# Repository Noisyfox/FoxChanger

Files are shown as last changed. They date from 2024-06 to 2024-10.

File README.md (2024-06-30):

# FoxChanger
[中文版点我](./README.chs.md)

Voron 2.4/Trident tool changer mod inspired by Prusa XL toolchanger.

No customized/homemade metal parts required, 100% off-the-shelf parts without any post-processing/modification, except for 3d-printed parts of course.

[Demo video](https://www.bilibili.com/video/BV1c142117zm)

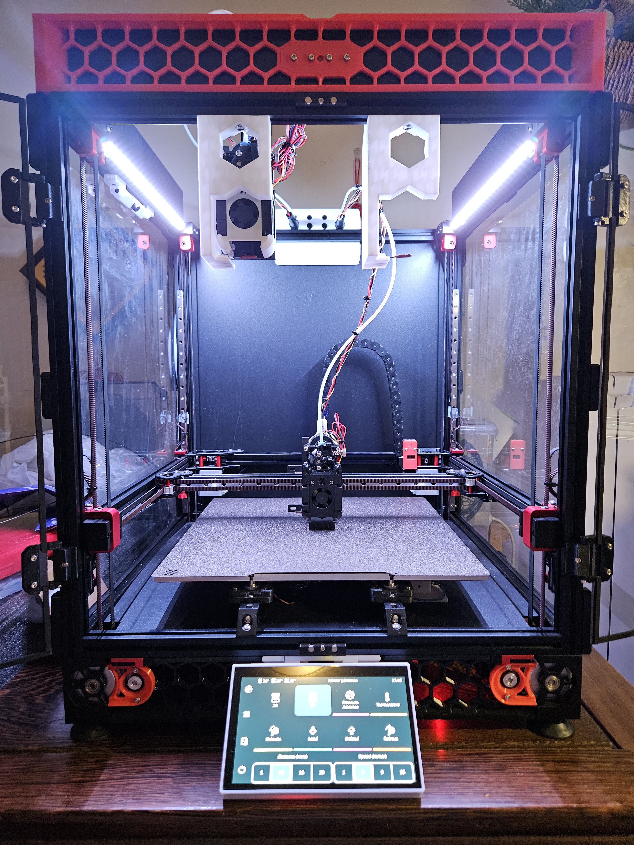
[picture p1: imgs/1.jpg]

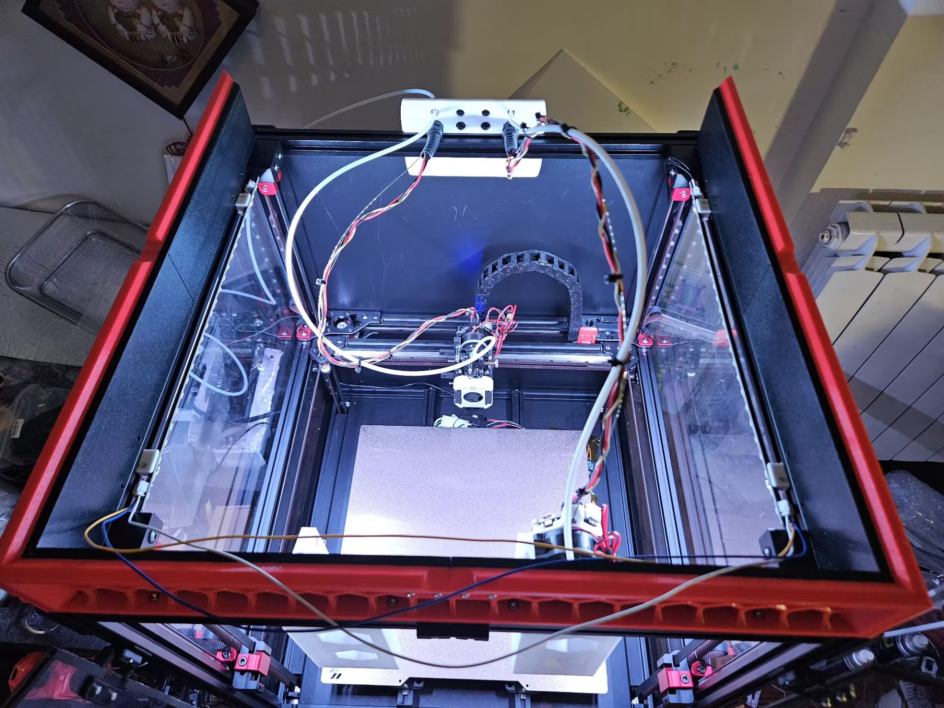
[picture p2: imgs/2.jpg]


# Credit
This project is based on the following excellent works:
- [VORON Design](https://vorondesign.com/)
- [Klipper](https://www.klipper3d.org/)
- [Prusa Research](https://www.prusa3d.com/) for their Prusa XL, that created this toolhead locking mechanism
- [Viesturs Zariņš](https://github.com/viesturz) for tapchanger, klipper-toolchanger and nozzle align
- [3DUnplugged](https://www.youtube.com/channel/UCr8K1tva2CaEhyqNyaEjq_w) for his excellent analysis on Prusa XL's toolchanger, and his DAKSH tool changer V2 design
- [diedirk](https://www.printables.com/@diedirk_282928) for Sherpa Zero ECAS extruder
- [KayosMaker](https://github.com/KayosMake) for canboard mount
- [chirpy2605](https://github.com/chirpy2605) for the DragonBurner toolhead

# Hardware Overview
This mod contains the following 3 parts:
- Toolchanger: toolhead mount and dock
- Piezo bed sensor: piezo based z homing sensor under heatbed
- Nozzle align probe: micro-switch based multi-toolhead alignment tool

## Toolchanger
Currently this mod is designed around the Dragon Burner. Other toolheads might be used with different mount, however the size constraint needs to be considered. Also there will be no space to install the z proble inside the toolhead, or use Voron Tap for z homing, so a BambuLab P1/X1-like heatbed piezo sensor is used instead.

__Note: All shop links are not affiliate links! Just for examples!__

- Unmodified [Dragon Burner](https://github.com/chirpy2605/voron/tree/main/V0/Dragon_Burner), except the mount
- A slightly modified version of [Sherpa Zero ECAS extruder](https://www.printables.com/model/495935-sherpa-zero-ecas), thicker to support cloned BMG gears without grinding the gear shaft
- [Fly SHT-36 V2 CAN board](https://mellow-3d.github.io/fly-sht36_v2_general.html)
- A slightly modified version of [KayosMaker's CANboard_Mounts](https://github.com/KayosMaker/CANboard_Mounts), with a grove to attach the umbilical steel wire
- X carriage
  - 6\*8\*3(inner\*outer\*height) sintered porous bronze bearing (x3)
  - 2\*25(PHi\*length) stainless steel round head cylindrical positioning pin (x4)
  - 1\*8(PHi\*length) stainless steel round head cylindrical positioning pin (x4)
  - 0.3\*3\*5(PHi\*outer\*length) 304 stainless steel spring (x4)
  - M3\*8 SHCS (x4)
  - M3\*12 SHCS (x2)
  - M3 heat set insert (x2)
- Toolhead mount
  - 1\*2\*8\*1(short\*long\*width\*thickness) steel angle with 3mm holes (x2)
  - 6\*4\*8\*M3 cone head positioning pin (x3)
  - M3\*2\*5(thread\*length\*outer diameter) brass round column with threaded throughhole (x4)
  - M3\*5 set screw DIN (x2)
  - 3\*30(PHi\*length) stainless steel round head cylindrical positioning pin (x2)
  - 6\*3(PHi\*thickness) round magnet (x2)
  - M3\*6 FSHC (x5)
  - M3 heat set insert (x4)
- Dock
  - 3\*50(PHi\*length) stainless steel round head cylindrical positioning pin (x2)
  - 6\*3(PHi\*height) round magnet (x2)
  - 0.4\*5\*15(thickness\*width\*length) 301 stainless steel strip
  - [nozzle pad mold from TapChanger](https://github.com/viesturz/tapchanger/tree/f6a354f5bf93b9d8721f022794a41ad3e51c5828/Dock/Jigs)
  - [High temperature silicone adhesive](https://www.aliexpress.com/item/1005002418580570.html)
  - M3\*6 FSHC (x2)
  - M3\*12 SHCS (x1)
  - M5\*10 BHCS (x1)
  - M3 heat set insert (x2)
  - M3 T-nut (x1)
  - M5 T-nut (x1)

Note: Due to the extended latch, the gantry left XY joint needs to be modified, or use the CNC version like I did.

## Piezo bed sensor
Heatbed z probe sensor made with 4 20mm piezo disks and an off-the-shelf analog vibration sensor board.

- Piezoelectric Shock Tap Sensor, Vibration Switch Module like [this one](https://www.amazon.com/Rakstore-Piezoelectric-Vibration-piezoelectric-Percussion/dp/B09GX97X6B)
- 20mm piezo disk (x4)
- 6\*8\*3(inner\*outer\*height) sintered porous bronze bearing (x8)
- 6\*15(PHi\*length) linear guide rail (x8)
- M3\*8 SHCS (x4)
- M3\*10 SHCS (x8)
- M3 heat set insert (x8)
- M3 T-nut (x4)

## Nozzle align probe

- 6mm stainless steel ball (or Si3N4 ball like I'm using) (x1)
- Omron D2FC-f-7N micro-switch, or any other compatiable ones (x1)
- 6\*8\*3(inner\*outer\*height) sintered porous bronze bearing (x1)

# Print
Print most of the parts with the same settings as what Voron recommended.

I print most parts in PETG, except the latch, x carriage frame, dragon burner back plate and piezo probes which are printed in PETG-CF.

Print the latches in 100% infill and Arachne wall generator.

Most of the parts are designed to be printed without support, and some of them have built-in support.

I'll provide recommended print orientation inside each part's readme.

# Support this project
If you like my work, feel free to by me a coffe:



[afdian](https://afdian.net/a/noisyfox)

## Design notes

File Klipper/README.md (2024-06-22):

[中文版点我](./README.chs.md)

# Klipper setup

The config here is just the setup I'm using.

## Installing

- Install [toolchanger extension](https://github.com/viesturz/klipper-toolchanger/)
- Use the config as a guide for your own config

## Orca Slicer config

### Printer settings
- Cooling tube length: 15
- Cooling tube position: 35
- Filament parking position: 35
- Enable filament ramming: false
- Change filament G-code:
```
M104 T[current_extruder] S[old_filament_temp] ; fix issue that current temp is set to next filament during unload
M104 T[next_extruder] S[new_filament_temp] ; preheating the next toolhead

M204 S9000
{if toolchange_count > 1 && (z_hop_types[current_extruder] == 0 || z_hop_types[current_extruder] == 3)}
G17
G2 Z{z_after_toolchange + 0.4} I0.86 J0.86 P1 F10000 ; spiral lift a little from second lift
{endif}

{if toolchange_count > 1}
T[next_extruder] X=[x_after_toolchange] Y=[y_after_toolchange] Z=[z_after_toolchange]
G1 X[x_after_toolchange] Y[y_after_toolchange] Z[z_after_toolchange] F12000 ; make gcode preview happy
{else}
T[next_extruder]
{endif}
```
- Start Gcode:
```
M104 S0
M140 S0
PRINT_START EXTRUDER=[nozzle_temperature_initial_layer] BED=[bed_temperature_initial_layer_single] CHAMBER=[chamber_temperature] MESH_MIN={adaptive_bed_mesh_min[0]},{adaptive_bed_mesh_min[1]} MESH_MAX={adaptive_bed_mesh_max[0]},{adaptive_bed_mesh_max[1]} MESH_ALGO=[bed_mesh_algo] MESH_PROB_COUNT={bed_mesh_probe_count[0]},{bed_mesh_probe_count[1]} TOOL=[initial_extruder]
```

### Filament settings
- Delay after unloading: 2

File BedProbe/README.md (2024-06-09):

[中文版点我](./README.chs.md)

## Install
1. Install the linear guide rail on the bottom part. Use fitting.STEP to help pushing the rails in.
2. Install the heat set and bronze bearing. Use ring_pusher.STEP from toolchanger to help pushing the bearing in. Avoid using any metal tools to push the bearing in, otherwise you might damage it and increasing the friction!
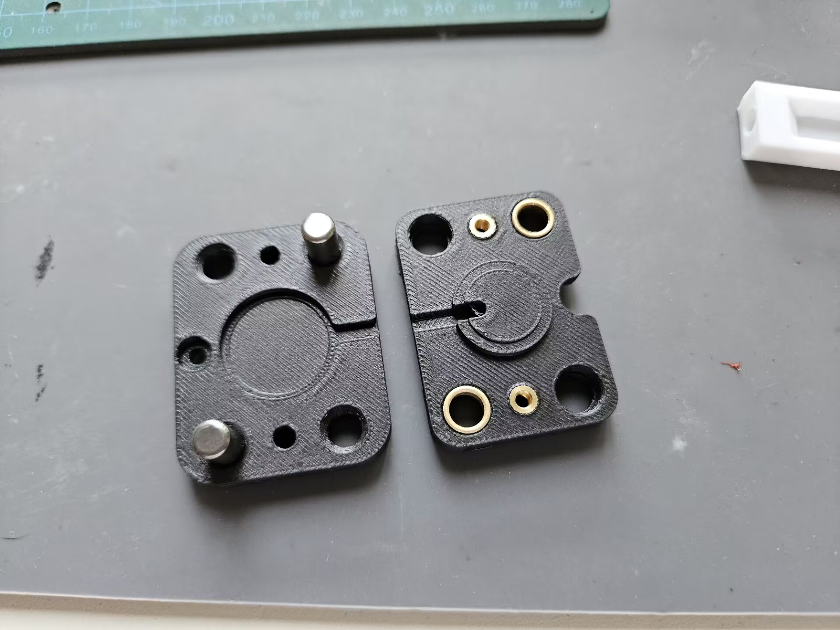
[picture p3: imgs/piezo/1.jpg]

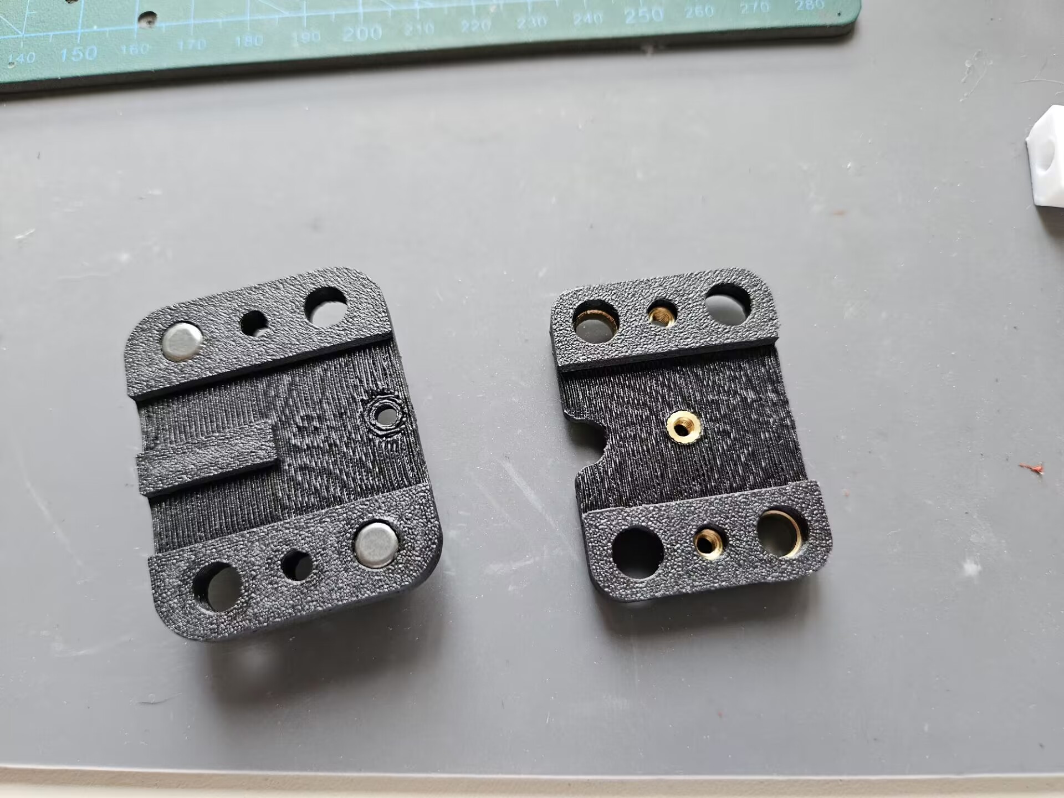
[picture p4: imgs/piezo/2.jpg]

3. Put the piezo disk in, make sure the ceramic side faces upwards
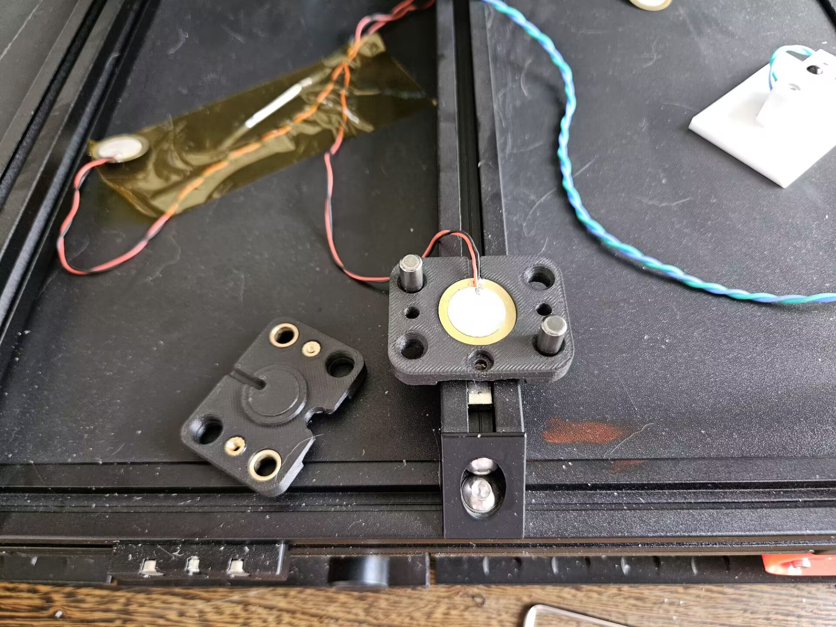
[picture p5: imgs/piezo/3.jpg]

4. Put on M3x10 screws. Do not tighten! The screws are here to avoid heatbed falling down when you flip the printer over, do not apply any extra pressure to the sensor.
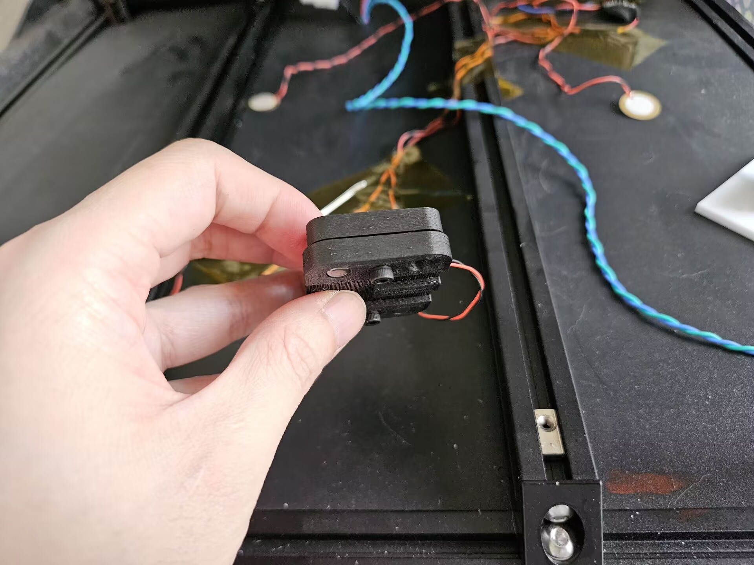
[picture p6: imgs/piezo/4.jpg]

5. Mount the sensors on the extrusions and connect the wires
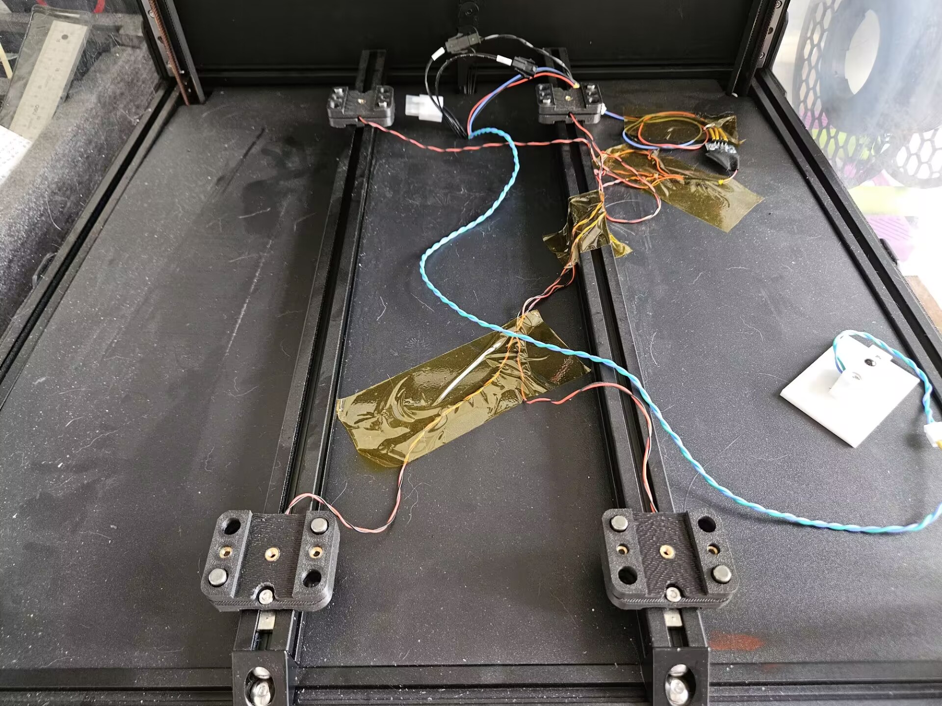
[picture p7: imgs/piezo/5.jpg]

6. Put the heatbed on
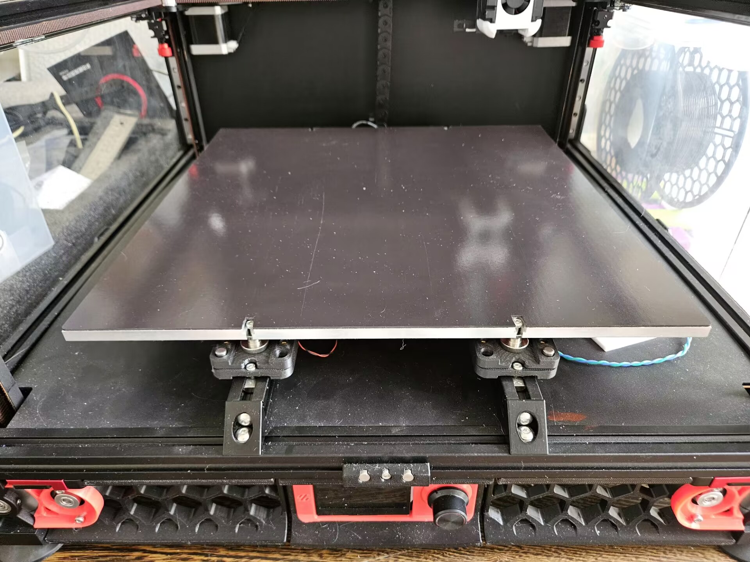
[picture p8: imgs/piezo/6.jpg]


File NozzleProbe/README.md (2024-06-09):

[中文版点我](./README.chs.md)

[Demo video](https://www.bilibili.com/video/BV1hH4y1u7oX/)

This is a simple but accurate nozzle alignment probe that works with [viesturz's NozzleAlign](https://github.com/viesturz/NozzleAlign).

Just clamp it to your heatbed and follows the instructions [here](https://github.com/viesturz/NozzleAlign/blob/main/README.md#klipper-integration).

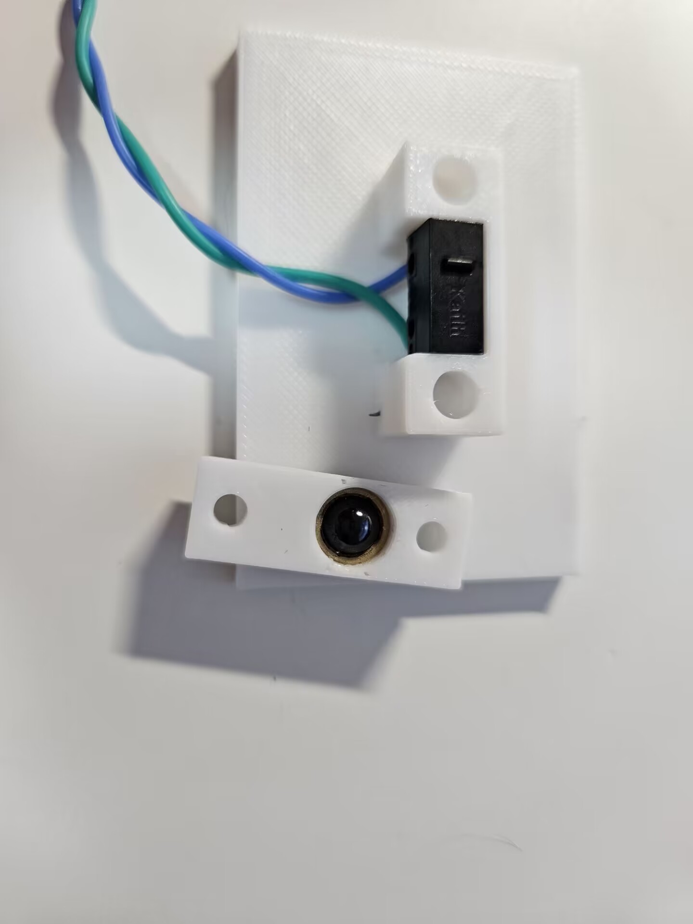
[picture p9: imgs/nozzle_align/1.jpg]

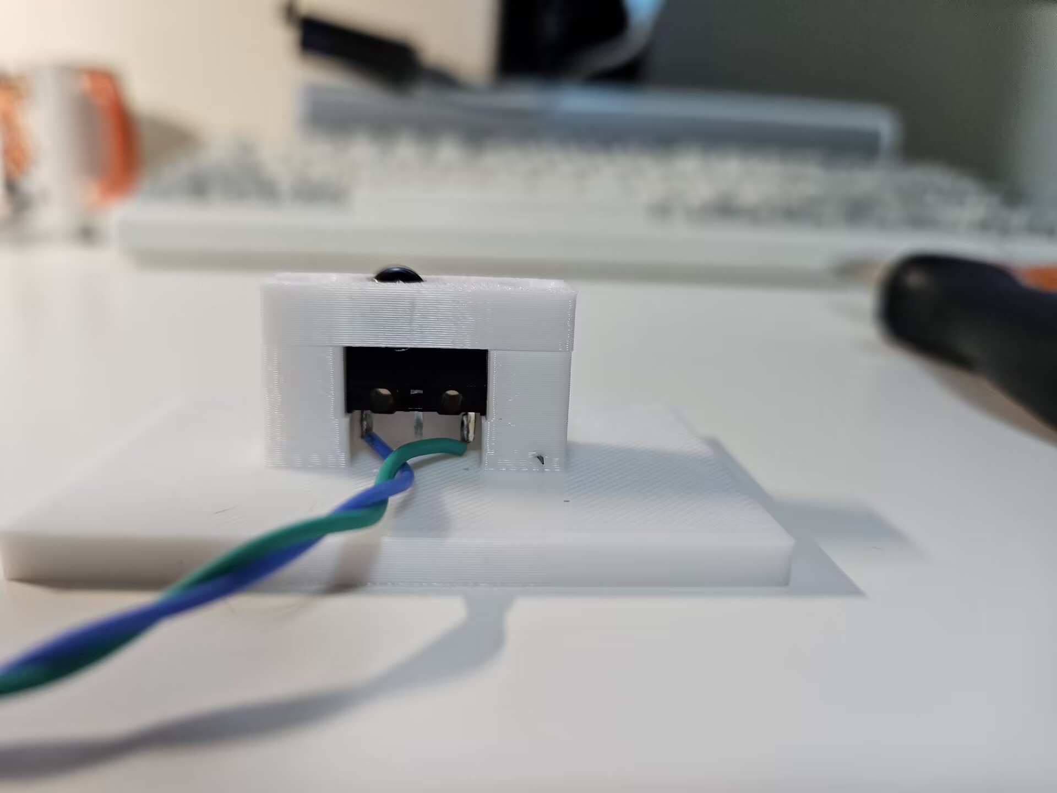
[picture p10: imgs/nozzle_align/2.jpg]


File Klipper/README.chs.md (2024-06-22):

[English](./README.md)

# Klipper配置

这些只是我在用的配置，经供参考。

## 安装

- 安装 [klipper toolchanger 插件](https://github.com/viesturz/klipper-toolchanger/)
- 参照我的配置来设置你的打印机

## Orca Slicer配置

### 打印机设置
- 喉管长度: 15
- 喉管位置: 35
- 耗材停靠位置: 35
- 启用耗材尖端成型: false
- 耗材丝更换 G-code:
```
M104 T[current_extruder] S[old_filament_temp] ; fix issue that current temp is set to next filament during unload
M104 T[next_extruder] S[new_filament_temp] ; preheating the next toolhead

M204 S9000
{if toolchange_count > 1 && (z_hop_types[current_extruder] == 0 || z_hop_types[current_extruder] == 3)}
G17
G2 Z{z_after_toolchange + 0.4} I0.86 J0.86 P1 F10000 ; spiral lift a little from second lift
{endif}

{if toolchange_count > 1}
T[next_extruder] X=[x_after_toolchange] Y=[y_after_toolchange] Z=[z_after_toolchange]
G1 X[x_after_toolchange] Y[y_after_toolchange] Z[z_after_toolchange] F12000 ; make gcode preview happy
{else}
T[next_extruder]
{endif}
```
- 打印机起始 Gcode:
```
M104 S0
M140 S0
PRINT_START EXTRUDER=[nozzle_temperature_initial_layer] BED=[bed_temperature_initial_layer_single] CHAMBER=[chamber_temperature] MESH_MIN={adaptive_bed_mesh_min[0]},{adaptive_bed_mesh_min[1]} MESH_MAX={adaptive_bed_mesh_max[0]},{adaptive_bed_mesh_max[1]} MESH_ALGO=[bed_mesh_algo] MESH_PROB_COUNT={bed_mesh_probe_count[0]},{bed_mesh_probe_count[1]} TOOL=[initial_extruder]
```

### 耗材丝设置
- 卸载后延迟: 2

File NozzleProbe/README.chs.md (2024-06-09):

[English](./README.md)

[演示视频](https://www.bilibili.com/video/BV1hH4y1u7oX/)

这是一个简单但是精准的喷嘴偏移校准传感器，配合[viesturz的NozzleAlign工具](https://github.com/viesturz/NozzleAlign)使用。

将它夹到热床上后，按照[这里的说明](https://github.com/viesturz/NozzleAlign/blob/main/README.md#klipper-integration)操作即可。




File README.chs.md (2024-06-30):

# FoxChanger
[English](./README.md)

Voron 2.4/Trident换头模组，类Prusa XL。

无需任何自制、定制金属件，完全由现成的标准五金件组成，且完全不需要后期加工。

[演示视频](https://www.bilibili.com/video/BV1c142117zm)




# 鸣谢
本项目基于和/或受到以下项目的启发与帮助:
- [VORON Design](https://vorondesign.com/)
- [Klipper](https://www.klipper3d.org/)
- [Prusa Research](https://www.prusa3d.com/)的Prusa XL, 给我们带来的这种换头的机械结构设计
- [Viesturs Zariņš](https://github.com/viesturz)的tapchanger, klipper-toolchanger和nozzle align
- [3DUnplugged](https://www.youtube.com/channel/UCr8K1tva2CaEhyqNyaEjq_w)对Prusa XL换头机构的详细分析，以及他的DAKSH tool changer V2设计也给我很大启发
- [diedirk](https://www.printables.com/@diedirk_282928)的Sherpa Zero ECAS挤出机
- [KayosMaker](https://github.com/KayosMake)的CAN板固定器
- [chirpy2605](https://github.com/chirpy2605)的DragonBurner工具头设计

# 硬件概览
本模组由以下3个部分组成:
- 换头模组: 换头机构和工具头停泊坞
- 压电热床: 基于压电蜂鸣器的热床归零传感器
- 喷嘴校准器: 基于微动开关的多头喷嘴偏移校准工具

## 换头模组
目前该换头机构基于Dragon Burner设计。理论上可以用在其它工具头上，但是需要注意空间限制。另外因为空间原因无法安装传统的调平传感器和Voron Tap，所以我用了一个和拓竹的P1/X1类似的压电热床传感器。

__请注意：所有商品链接只是为了举例，与本人没有任何利益关系！__（当然我现在在用的零件也是从这些链接里买的就是了）

- 原版 [Dragon Burner](https://github.com/chirpy2605/voron/tree/main/V0/Dragon_Burner)
- 一个稍微修改过的[Sherpa Zero ECAS extruder](https://www.printables.com/model/495935-sherpa-zero-ecas)，加厚了一点用来兼容市面上常见的第三方BMG挤出机齿轮组，而不需要打磨轴
- [Fly SHT-36 V2 CAN工具板](https://mellow-3d.github.io/fly-sht36_v2_general.html)
- 一个稍微修改过的[KayosMaker's CANboard_Mounts](https://github.com/KayosMaker/CANboard_Mounts)，加了一个用来固定线缆导向钢丝的槽
- X滑车端
  - 6\*8\*3(内径\*外径\*高) [黄铜粉末冶金含油轴承](https://item.taobao.com/item.htm?id=696124179286&skuId=4938962921704) (x3)
  - 2\*25(直径\*长) [不锈钢圆柱定位销](https://detail.tmall.com/item.htm?id=599565830368&skuId=4449932305487) (x4)
  - 1\*8(直径\*长) [不锈钢圆柱定位销](https://detail.tmall.com/item.htm?id=599565830368&skuId=4449932305485) (x4)
  - 0.3\*3\*5(线径\*外径\*长) [304不锈钢压簧](https://detail.tmall.com/item.htm?id=684011040182&skuId=4894464993901) (x4)
  - M3\*8 SHCS 螺丝 (x4)
  - M3\*12 SHCS 螺丝 (x2)
  - M3 热熔螺母 (x2)
- 工具头端
  - 1\*2\*8\*1(短边\*长边\*宽\*厚) [1/2角铁3MM孔](https://detail.tmall.com/item.htm?id=609920972548&skuId=5025597343138) (x2)
  - 6\*4\*8\*M3 [锥头定位销](https://item.taobao.com/item.htm?id=629688584816&skuId=4652635966160) (x3)
  - M3\*2\*5(螺纹\*长\*外径) [内螺纹圆铜柱](https://detail.tmall.com/item.htm?id=718349103139&skuId=5012741965543) (x4)
  - M3\*5 [平端内六角紧定螺丝](https://detail.tmall.com/item.htm?id=669353260796&skuId=5037115490335) (x2)
  - 3\*30(直径\*长) [不锈钢圆柱定位销](https://detail.tmall.com/item.htm?id=599565830368&skuId=4980360758229) (x2)
  - 6\*3(直径\*厚) [圆形磁铁](https://item.taobao.com/item.htm?id=650582587437&skuId=4683250052175) (x2)
  - M3\*6 FSHC 螺丝 (x5)
  - M3 热熔螺母 (x4)
- 工具头停泊坞
  - 3\*50(直径\*长) [不锈钢圆柱定位销](https://detail.tmall.com/item.htm?id=599565830368&skuId=4980360758219) (x2)
  - 6\*3(直径\*厚) [圆形磁铁](https://item.taobao.com/item.htm?id=650582587437&skuId=4683250052175) (x2)
  - 0.4\*5\*15(厚\*宽\*长) [301弹簧钢带](https://item.taobao.com/item.htm?id=617939955067&skuId=4529325587657)
  - [来自TapChanger的喷嘴堵头模具](https://github.com/viesturz/tapchanger/tree/f6a354f5bf93b9d8721f022794a41ad3e51c5828/Dock/Jigs)
  - [耐高温硅密封胶](https://detail.tmall.com/item.htm?id=631534616231&skuId=4504220328741)
  - M3\*6 FSHC 螺丝 (x2)
  - M3\*12 SHCS 螺丝 (x1)
  - M5\*10 BHCS 螺丝 (x1)
  - M3 热熔螺母 (x2)
  - M3 T型滑块钢珠螺母 (x1)
  - M5 T型滑块钢珠螺母 (x1)

注意：由于两边伸出来的锁定滑块，龙门架的左侧XY轴连接器需要开槽，或者和我一样用CNC的版本。

## 压电热床传感器
由4片20mm压电蜂鸣器和震动传感器模块做的热床归零传感器。

- [压电震动传感器](https://detail.tmall.com/item.htm?id=652122497796)
- 20mm 压电蜂鸣片 (x4)
- 6\*8\*3(内径\*外径\*高) [黄铜粉末冶金含油轴承](https://item.taobao.com/item.htm?id=696124179286&skuId=4938962921704) (x8)
- 6\*15(直径\*长) [光轴](https://detail.tmall.com/item.htm?id=680516964370&skuId=4882059537337) (x8)
- M3\*8 SHCS 螺丝 (x4)
- M3\*10 SHCS 螺丝 (x8)
- M3 热熔螺母 (x8)
- M3 T型滑块钢珠螺母 (x4)

## 喷嘴校准器

- 6mm 钢珠 (或者像我在用的[氮化硅陶瓷滚珠](https://item.taobao.com/item.htm?id=689926834804&skuId=5083796203976)) (x1)
- [欧姆龙 D2FC-f-7N 微动](https://item.taobao.com/item.htm?id=574796579888&skuId=3774524789330)，或者任意相同尺寸的微动 (x1)
- 6\*8\*3(内径\*外径\*高) [黄铜粉末冶金含油轴承](https://item.taobao.com/item.htm?id=696124179286&skuId=4938962921704) (x1)

# 打印
大部分打印件遵循Voron官方建议打印参数打印。

大部分的件我是用的PETG打印的；锁定插销，X轴滑车，Dragon Burner背板和热床传感器用的PETG-CF。

打印锁定插销时建议使用100%填充以及Arachne墙生成器。

大部分打印件都不需要支撑便可打印，少部分打印件有设计内置支撑结构，需要在组装时移除。

每个组件的说明里将提供建议的打印摆放朝向，以供参考。

# 支持本项目
如果你喜欢我的工作，可以考虑支持我:



[afdian](https://afdian.net/a/noisyfox)

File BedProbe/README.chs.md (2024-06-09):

[English](./README.md)

## 安装
1. 在下半部分安装光轴。用fitting.step来在插入光轴时辅助固定。
2. 安装热熔螺母和铜轴套。用toolchanger/ring_pusher.STEP来插入轴套。避免用任何硬质工具，否则可能会损伤轴套导致阻力增加！


3. 放入蜂鸣片，注意有陶瓷的一面朝上。

4. 拧上M3x10螺丝。不要拧紧！螺丝只是为了防止你在翻转打印机时热床脱落，不要对传感器施加任何压力。

5. 把传感器固定到型材上，并接好导线。

6. 拧上热床。


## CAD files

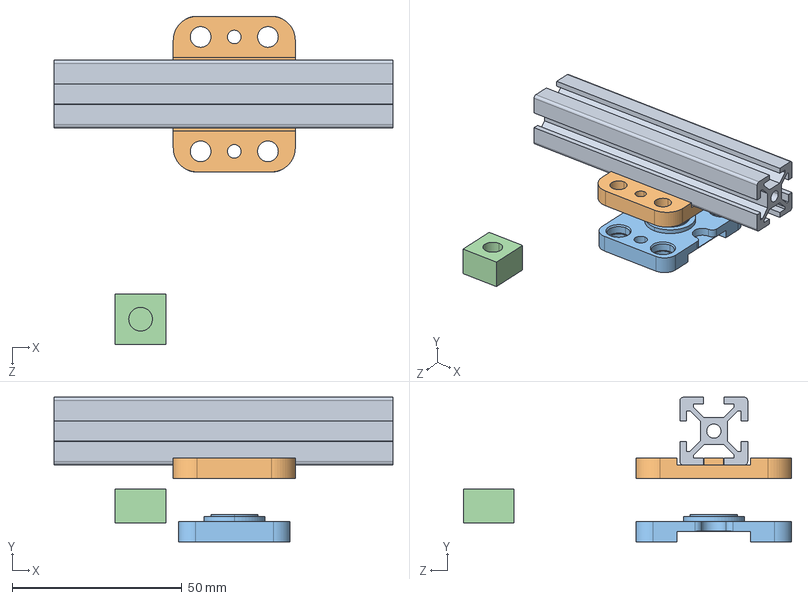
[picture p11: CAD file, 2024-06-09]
BedProbe/CAD/piezo.STEP
100.0 x 42.7 x 96.8 mm
BaseModel20240604214603
bottom
top
fitting

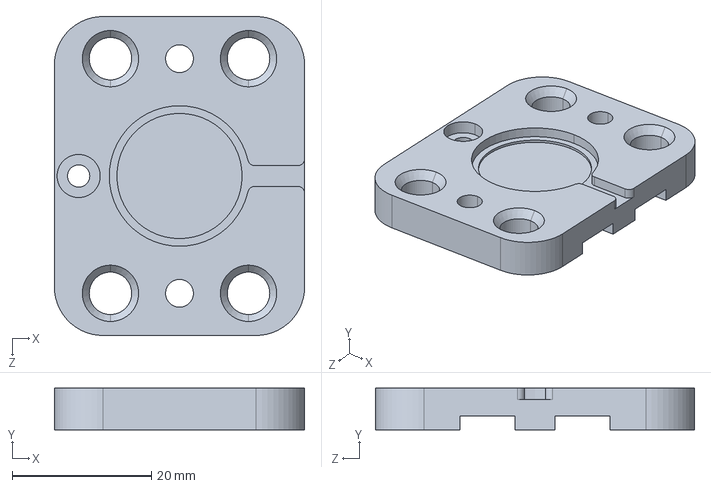
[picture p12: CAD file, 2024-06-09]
BedProbe/STLs/bottom.STEP
36.0 x 6.00 x 45.9 mm

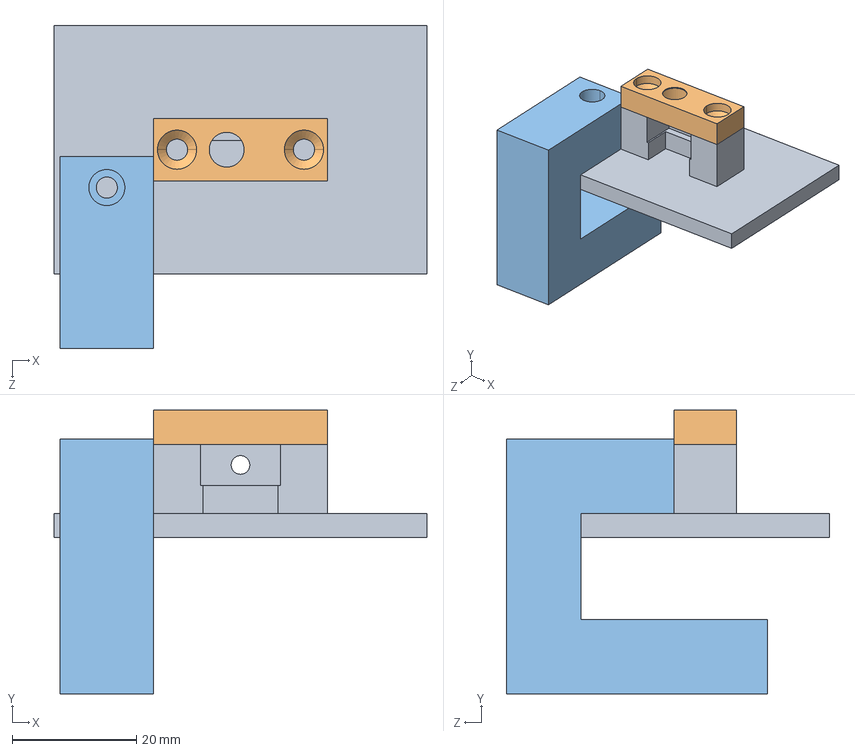
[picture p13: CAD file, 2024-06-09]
NozzleProbe/CAD/probe.STEP
60.0 x 45.7 x 52.0 mm
probe_base
lid
probe_clamp

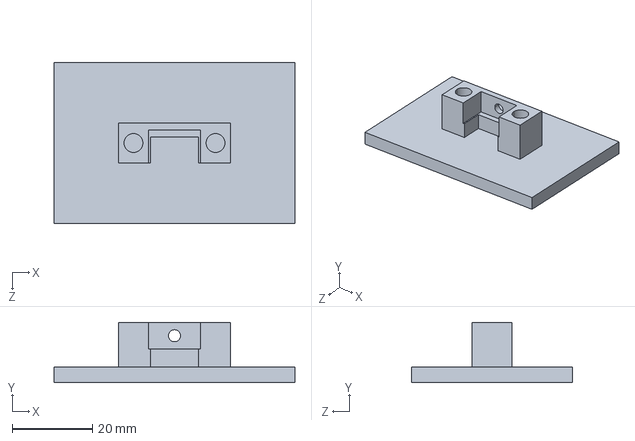
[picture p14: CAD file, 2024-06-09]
NozzleProbe/STLs/probe_base.STEP
60.0 x 15.0 x 40.0 mm

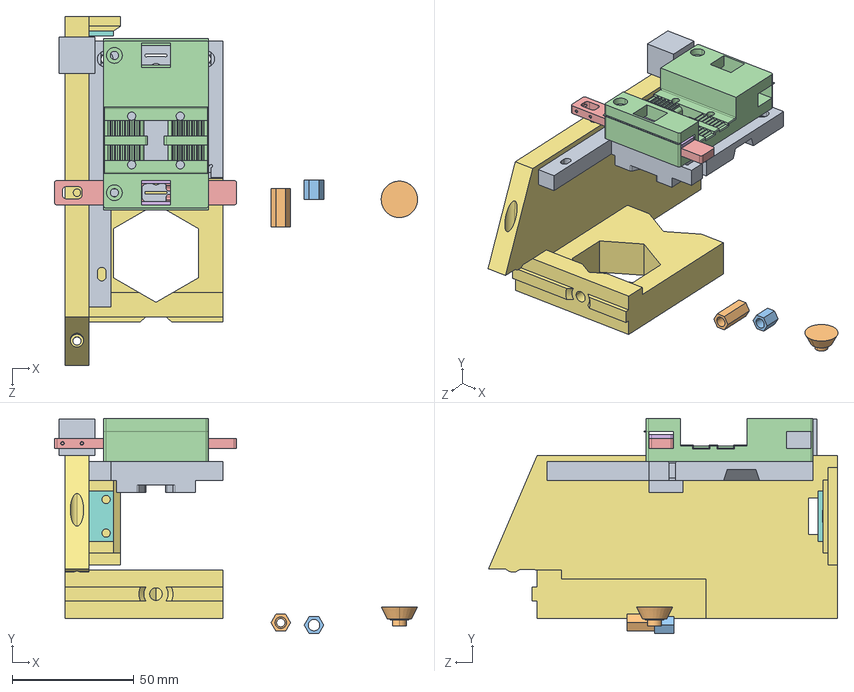
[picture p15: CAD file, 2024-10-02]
Toolchanger/CAD/toolchanger.STEP
149.5 x 88.6 x 143.6 mm
dragon_burner_back_plate
15.8mm_oct_spacer
8mm_oct_spacer
x_carriage_frame
latch
latch_press
head_holder
pad_clip
insert_tool
ring_pusher

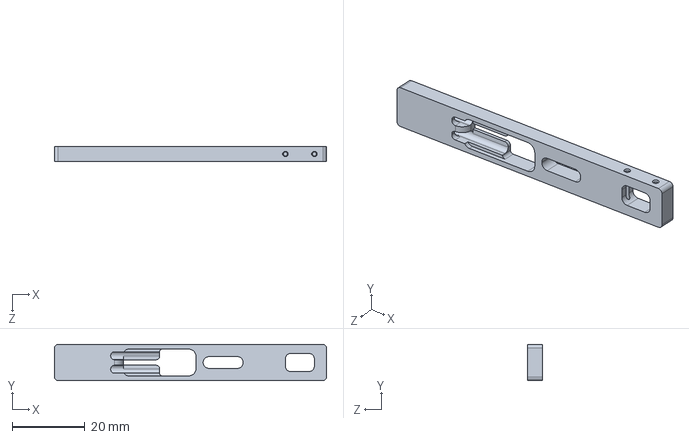
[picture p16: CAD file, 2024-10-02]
Toolchanger/STLs/latch.STEP
75.0 x 10.0 x 4.00 mm

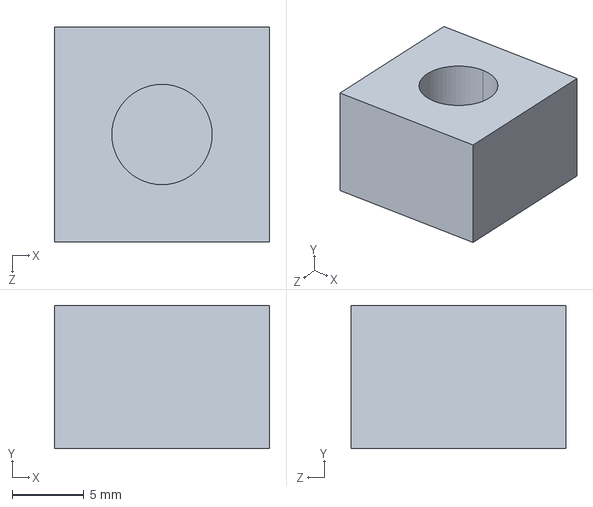
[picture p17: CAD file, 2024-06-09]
BedProbe/STLs/fitting.STEP
15.0 x 10.0 x 15.0 mm

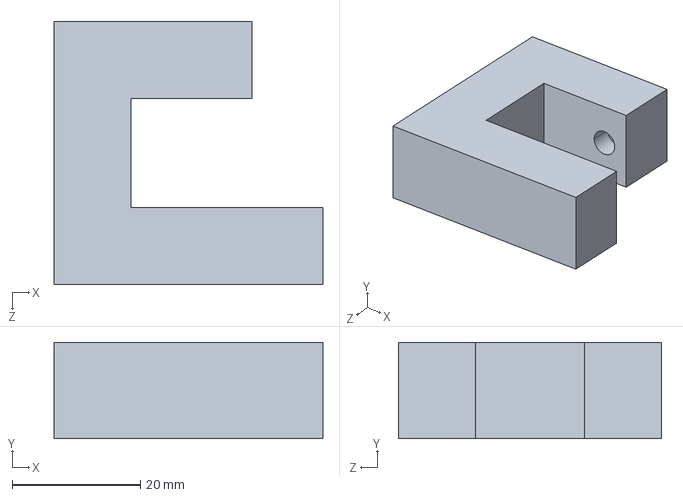
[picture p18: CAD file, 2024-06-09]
NozzleProbe/STLs/probe_clamp.STEP
42.0 x 15.0 x 41.0 mm

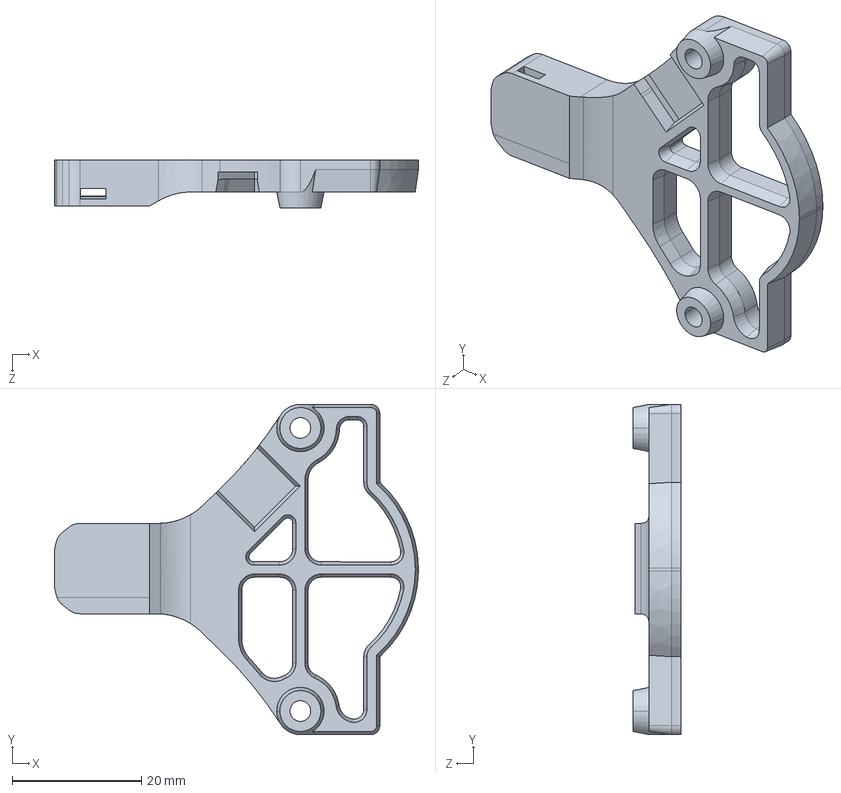
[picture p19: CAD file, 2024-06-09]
Toolchanger/CAD/STH-36_sherpa_mini_mounting_plate_overmold_strain.STEP
56.4 x 51.2 x 7.50 mm

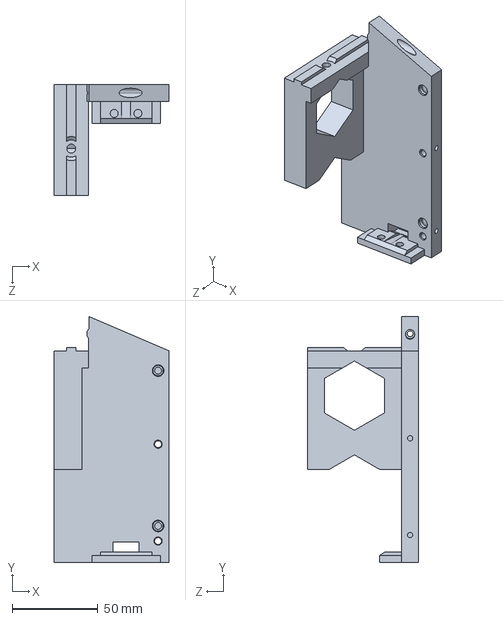
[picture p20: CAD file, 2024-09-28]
Toolchanger/STLs/head_holder.STEP
67.0 x 143.6 x 65.0 mm

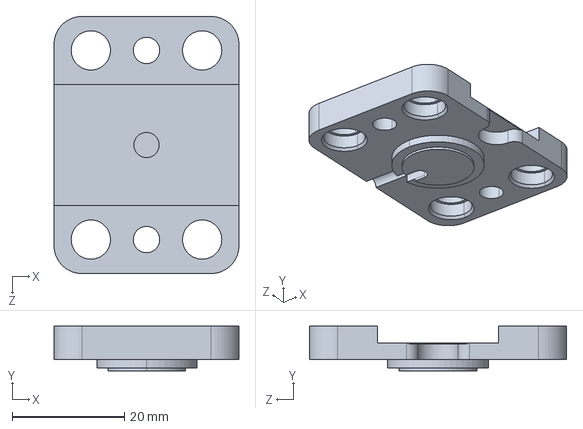
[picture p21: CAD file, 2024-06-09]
BedProbe/STLs/top.STEP
33.0 x 8.00 x 45.9 mm

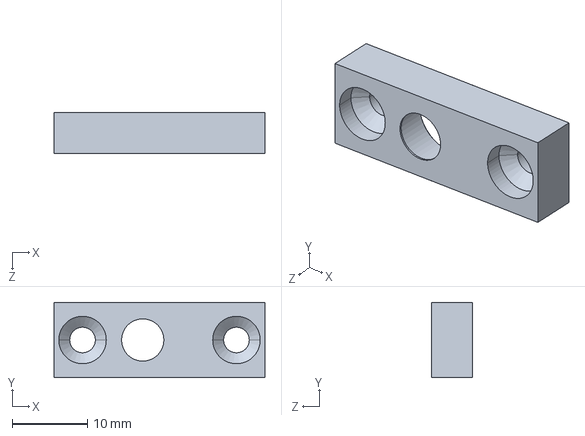
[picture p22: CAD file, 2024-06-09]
NozzleProbe/STLs/lid.STEP
28.0 x 10.0 x 5.50 mm

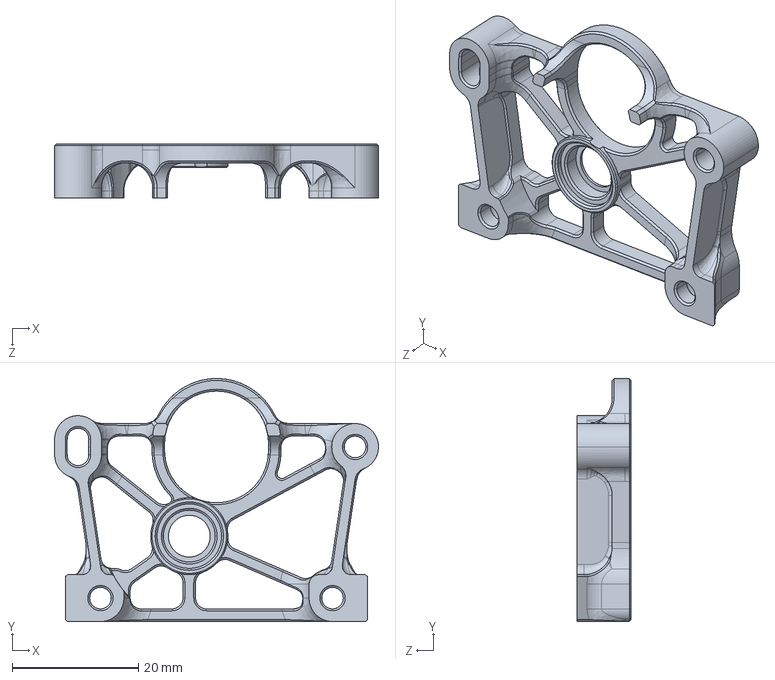
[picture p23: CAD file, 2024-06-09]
Toolchanger/CAD/housing_rear_nema14^housing_sherpa_mini_a3_r9c.STEP
51.2 x 38.4 x 8.60 mm

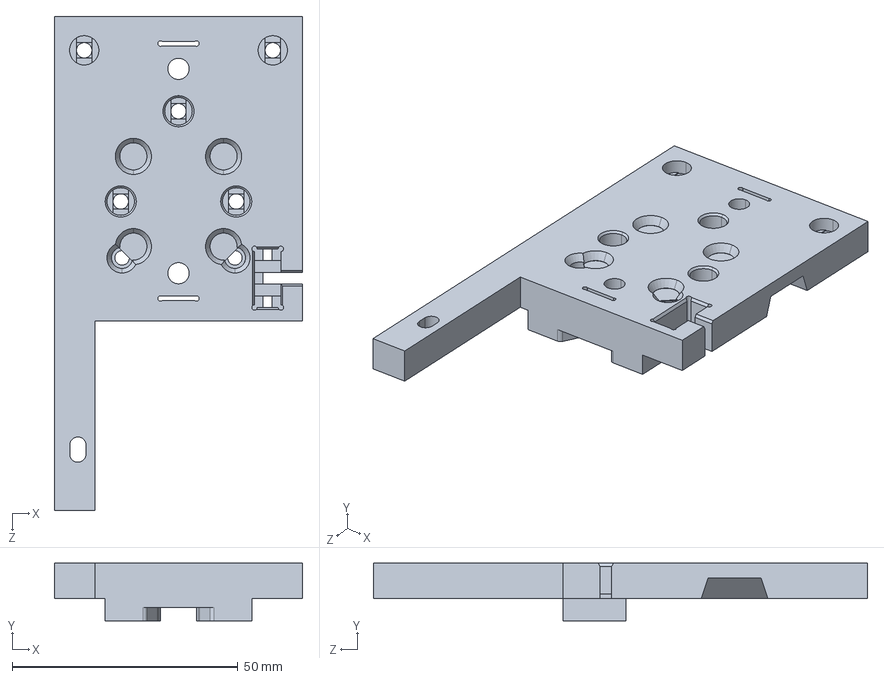
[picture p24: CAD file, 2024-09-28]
Toolchanger/STLs/dragon_burner_back_plate.STEP
55.0 x 12.8 x 109.5 mm

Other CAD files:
Toolchanger/STLs/latch_press.STEP
Toolchanger/STLs/x_carriage_frame.STEP
Toolchanger/STLs/15.8mm_oct_spacer.STEP
Toolchanger/STLs/ring_pusher.STEP
Toolchanger/STLs/8mm_oct_spacer.STEP
Toolchanger/STLs/insert_tool.STEP
Toolchanger/STLs/pad_clip.STEP

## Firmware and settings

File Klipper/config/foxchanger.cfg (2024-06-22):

[gcode_macro _FoxChanger_Variables]
description: Variables for FoxChanger

variable_tools:[0,1]

variable_normal_speed: 300    # in mm/s
variable_approach_speed: 10   # in mm/s

variable_latch_travel: 10            # in mm
variable_latch_pin_safe_y_offset: 15 # in mm
variable_tool_safe_y_offset: 100      # in mm
variable_tool_plug_offset: 12        # in mm
variable_carriage_safe_y_offset: 25  # in mm
variable_tool_safe_z: 160      # in mm, below this z the toolhead has no chance to collide with the dock. Set to 0 for trident

# Do not modify below
gcode:


[toolchanger]
  initialize_on: first-use
  uses_axis: xyz
  on_axis_not_homed: home
  initialize_gcode:
    _FOXCHANGER_INIT_BY_DETECTING_TOOL

  after_change_gcode:
    {% set tn = "T"+(tool.tool_number|string) %}
    {% if printer["gcode_macro " + tn ] %}
       SET_GCODE_VARIABLE MACRO={tn} VARIABLE=color VALUE="'c44'"
    {% endif %}
    {% if tool.params_input_shaper_freq_x %}
      SET_INPUT_SHAPER SHAPER_FREQ_X={tool.params_input_shaper_freq_x} SHAPER_FREQ_Y={tool.params_input_shaper_freq_y}
    {% endif %}

  dropoff_gcode:
    {% set fc_variables = printer["gcode_macro _FoxChanger_Variables"] %}
    {% set normal_speed = fc_variables.normal_speed * 60 | float %} 
    {% set approach_speed = fc_variables.approach_speed * 60 | float %} 
    {% set latch_travel = fc_variables.latch_travel | float %} 
    {% set latch_pin_safe_y_offset = fc_variables.latch_pin_safe_y_offset | float %} 
    {% set tool_safe_y_offset = fc_variables.tool_safe_y_offset | float %} 
    {% set tool_plug_offset = fc_variables.tool_plug_offset | float %} 
    {% set carriage_safe_y_offset = fc_variables.carriage_safe_y_offset | float %} 
    
    {% set max_z = printer.configfile.config["stepper_z"]["position_max"]|float %}
    {% set cur_z = printer.toolhead.position[2]|float %}
    
    {% set x_docked = tool.params_park_x | float %} 
    {% set y_docked = tool.params_park_y | float %} 
    {% set z_docked = tool.params_park_z | float %} 

    G90
    
    G0 F{normal_speed}
    
    ; Move 1 mm up to avoid crashing into things
    G0 Z{ [cur_z+1.0, max_z]|min }
    
    G0 X{x_docked + latch_travel} Y{y_docked + tool_safe_y_offset}  # align the toolhead in x axis, while avoid collision
    G0 Z{z_docked}                                                  # align in z axis
    G0 Y{y_docked + latch_pin_safe_y_offset}                        # move towards docking position stage 1, fast

    G0 Y{y_docked} F{approach_speed}                                # move towards final docking position, slow
    G0 X{x_docked}                                                  # release the latch
    G0 X{x_docked - 1}                                              # go back a little bit to make clearance between the pin and the latch hole
    G0 Y{y_docked + tool_plug_offset}                               # release the toolhead

    G0 F{normal_speed}
    
    G0 Y{y_docked + carriage_safe_y_offset}                         # move the carriage away

    M400                                                            # wait for movement complete
    _FOXCHANGER_ENSURE_TOOL_STATUS T={tool.tool_number} S=0         # make sure current tool has been detached
    
  
  pickup_gcode:
    {% set fc_variables = printer["gcode_macro _FoxChanger_Variables"] %}
    {% set normal_speed = fc_variables.normal_speed * 60 | float %} 
    {% set approach_speed = fc_variables.approach_speed * 60 | float %} 
    {% set latch_travel = fc_variables.latch_travel | float %} 
    {% set latch_pin_safe_y_offset = fc_variables.latch_pin_safe_y_offset | float %} 
    {% set tool_safe_y_offset = fc_variables.tool_safe_y_offset | float %} 
    {% set tool_plug_offset = fc_variables.tool_plug_offset | float %} 
    {% set carriage_safe_y_offset = fc_variables.carriage_safe_y_offset | float %} 
    
    {% set x_docked = tool.params_park_x | float %} 
    {% set y_docked = tool.params_park_y | float %} 
    {% set z_docked = tool.params_park_z | float %} 

    G90
    
    G0 F{normal_speed}
    G0 X{x_docked} Y{y_docked + carriage_safe_y_offset}  # align the toolhead in x axis, while avoid collision
    G0 Z{z_docked - 0.3}                                 # align in z axis, while account for the z drop when docked

    # Wait for temp before actually picking up the tool, while the nozzle is resting on it's pad.
    {% if tool.extruder %}
      TEMPERATURE_WAIT SENSOR={printer.toolhead.extruder} MINIMUM={printer[tool.extruder].target}
    {% endif %}

    G0 Y{y_docked - 0.5} F{approach_speed}               # move towards toolhead
    G0 X{x_docked + latch_travel + 1}                    # close the latch
    G0 X{x_docked + latch_travel}                        # go back a little bit to make clearance between the pin and the latch hole
    
    G0 F{normal_speed}
    
    G0 Y{y_docked + tool_safe_y_offset}                  # move the toolhead away

    M400                                                            # wait for movement complete
    _FOXCHANGER_ENSURE_TOOL_STATUS T={tool.tool_number} S=1         # make sure current tool has been attached

    # Restore the position
    {% set restore_params = "" %}
    {% if 'X' in restore_position %}
      {% set restore_params = restore_params ~ " X="~restore_position.X %}
    {% endif %}
    {% if 'Y' in restore_position %}
      {% set restore_params = restore_params ~ " Y="~restore_position.Y %}
    {% endif %}
    {% if 'Z' in restore_position %}
      {% set restore_params = restore_params ~ " Z="~restore_position.Z %}
    {% endif %}

    {% if restore_params != "" %}
      _FOXCHANGER_SAFEMOVE{restore_params} F={normal_speed}
    {% endif %}

[gcode_macro _FOXCHANGER_INIT_BY_DETECTING_TOOL]
gcode:
  {% set fc_variables = printer["gcode_macro _FoxChanger_Variables"] %}
  {% set allTools = fc_variables.tools %}
  
  # Detect current tool
  {% set ns = namespace(found=false) %}
  {% set ns.current_tool = -1 %}
  {% for tool in allTools %}
    {% if printer["gcode_button T"~tool~"_check"].state == "PRESSED" %}
      RESPOND MSG="{"Tool " ~tool ~" is active"}"
      {% if ns.current_tool != -1 and ns.current_tool != tool %}
        { action_raise_error("Multiple active toolheads detected!") }
      {% endif %}
      {% set ns.current_tool = tool %}
    {% else %}
      RESPOND MSG="{"Tool " ~tool ~" is inactive"}"
    {% endif %}
  {% endfor %}

  {% if ns.current_tool == -1 %}
    { action_raise_error("No active toolhead detected!") }
  {% endif %}
  
  RESPOND MSG="{"Current active tool: " ~ns.current_tool}"
  INITIALIZE_TOOLCHANGER T={ns.current_tool}

[gcode_macro _FOXCHANGER_ENSURE_TOOL_STATUS]
description: T=<index> S=<status>
  Ensure given tool is detached(0)/attached(1).
gcode:
  {% set status = printer["gcode_button T"~params.T~"_check"].state == "PRESSED" %}
  {% if status %}
    RESPOND MSG="{"Tool " ~params.T ~" is active"}"
    {% if params.S != "1" %}
      { action_raise_error("Expect tool " ~params.T ~" to be detached, but it's not!") }
    {% endif %}
  {% else %}
    RESPOND MSG="{"Tool " ~params.T ~" is inactive"}"
    {% if params.S != "0" %}
      { action_raise_error("Expect tool " ~params.T ~" to be attached, but it's not!") }
    {% endif %}
  {% endif %}
  

[gcode_macro _FOXCHANGER_SAFEMOVE]
description: [X=<pos>] [Y=<pos>] [Z=<pos>] [F=<rate>]
  Safe move the toolhead to given position after tool change
gcode:
  {% set fc_variables = printer["gcode_macro _FoxChanger_Variables"] %}
  {% set tool_safe_y_offset = fc_variables.tool_safe_y_offset|float %} 
  {% set tool_safe_z = fc_variables.tool_safe_z|float %} 
  
  {% set tool = printer[printer.toolchanger.tool] %}
  {% set y_docked = tool.params_park_y|float %} 
  
  {% set cur_x = printer.toolhead.position[0]|float %}
  {% set cur_y = printer.toolhead.position[1]|float %}
  {% set cur_z = printer.toolhead.position[2]|float %}

  {% set target_y = cur_y %}
  {% set target_z = cur_z %}
  {% if 'Y' in params %}
    {% set target_y = params.Y|float %}
  {% endif %}
  {% if 'Z' in params %}
    {% set target_z = params.Z|float %}
  {% endif %}
  
  # Check dangerous movement
  {% set tool_safe_y = y_docked + tool_safe_y_offset %}
  {% if target_y < tool_safe_y and target_z > tool_safe_z %}
    { action_raise_error("Unable to safely move to the position ("~cur_x~","~target_y~","~target_z~")! Toolhead could crash!") }
  {% endif %}

  {% if 'F' in params %}
    G0 F{params.F}
  {% endif %}

  # Avoid collision
  {% if target_y < tool_safe_y and cur_z > tool_safe_z %}
    G0 Z{tool_safe_z}
  {% endif %}

  # Move to the given position with smooth rounded move.
  {% if 'X' in params %}
    ROUNDED_G0 X={params.X} D=1000
  {% endif %}
  {% if 'Y' in params %}
    ROUNDED_G0 Y={params.Y} D=0
  {% endif %}
  {% if 'Z' in params %}
    ROUNDED_G0 Z={params.Z} D=150
  {% endif %}
  ROUNDED_G0 D=0
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

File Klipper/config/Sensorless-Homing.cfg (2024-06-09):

# This configuration file contains variables and macros specific for homing X and Y using stallguard rather than 
# physical switches. You will likely need to have DIAG jumpers installed on your mainboard and Klipper configured
# correctly for this to work.
# 
# More information can be found here: https://www.klipper3d.org/TMC_Drivers.html?h=sens#sensorless-homing
# 
# Be sure to [include] this .cfg file in printer.cfg **BEFORE** you have working SGTHRS/SGT values for
# [tmcXXXX stepper_x] and [tmcXXXX stepper_y] as that will simplify this process. If you already have SGTHRS/SGT
# values in your config, they will likely need adjusting after enabling this configuration.
# 
### Default motor current and homing speed are configured per axis in printer.cfg ###
# 
##################################
## XY Sensorless Homing Variables:

[gcode_macro _Sensorless_Homing_Variables]
description: Variables for sensorless homing X and Y

variable_homing_current: 0.0                # The desired motor current for homing the X and Y axes. Leave as '0.0' to use run_current values instead.
variable_clear_time: 1                      # Time in seconds to wait for stallguard registers to clear, default is 1 second.
variable_x_backoff_distance: 5              # Distance in mm to back off from the X axis after homing.
variable_y_backoff_distance: 5              # Distance in mm to back off from the Y axis after homing.
variable_z_hop_distance: 10                 # Distance to move Z axis prior to homing, and after homing.
variable_first_homed_axis: 'Y'              # First axis to home when 'G28' is called. Some prefer homing Y before X.

## The following variables are used for moving the printhead to a certain part of the bed before homing the Z axis:

variable_safe_z_enable: True                # Enables/disables moving the printhead before homing the Z axis.
variable_safe_x: -128                       # Safe X position to home the Z axis, leave at -128 to home to the center of the X axis.
variable_safe_y: -128                       # Safe Y position to home the Z axis, leave at -128 to home to the center of the Y axis.

# Do not modify below
gcode:

[gcode_macro _HOME_X]
gcode:

    {% set sensorless_variables = printer["gcode_macro _Sensorless_Homing_Variables"] %}            # Pull variables from _Sensorless_Homing_Variables
    {% set homing_current = sensorless_variables.homing_current | float %}                          #
    {% set backoff_distance = sensorless_variables.x_backoff_distance | float %}                    #
    {% set clear_time = (sensorless_variables.clear_time * 1000) | float %}                         #

    {% set positive_dir = printer.configfile.settings.stepper_x.homing_positive_dir | abs %}        # Pull X axis homing speed from config
    {% set homing_speed = (printer.configfile.settings['stepper_x'].homing_speed * 60) | float %}   #

    {% if homing_current != 0.0 %}                                                                  # If a homing_current is defined, do the following:
      {% if 'y' not in printer.toolhead.homed_axes %}                                               # Check if the Y axis is not homed, if Y is not homed,
        SET_TMC_CURRENT STEPPER=stepper_x CURRENT={homing_current}                                  # set the homing_current
        SET_TMC_CURRENT STEPPER=stepper_y CURRENT={homing_current}                                  #
      {% elif 'x' in printer.toolhead.homed_axes %}                                                 # 
        SET_TMC_CURRENT STEPPER=stepper_x CURRENT={homing_current}                                  # If X is already homed but is requested to home again,
        SET_TMC_CURRENT STEPPER=stepper_y CURRENT={homing_current}                                  # set the homing_current
      {% endif %}                                                                                   #
    {% endif %}                                                                                     #

    G4 P{clear_time}                                                                                # Wait for stallguard registers to clear

    G28 X                                                                                           # Home the X axis

    {% if backoff_distance > 0 %}                                                                   # Check if variable_backoff_distance is greater than 0, and back off from axis
      {% if positive_dir == True %}                                                                 # Check if the axis is homed in the positive direction
        G91                                                                                         # If it is, back away in the negative direction
        G0 X-{backoff_distance} F{homing_speed}                                                     #
        G90                                                                                         #
      {% else %}                                                                                    #
        G91                                                                                         # If the axis is not homed in the positive direction,
        G0 X{backoff_distance} F{homing_speed}                                                      # back away in the positive direction
        G90                                                                                         #
      {% endif %}                                                                                   #
    {% endif %}                                                                                     #

    {% if positive_dir == True %}                                                                   # Check if homing direction is positive
      G0 X{printer.configfile.settings.stepper_x.position_endstop - backoff_distance}               # Set X axis position to remove offset incurred from sensorless homing
    {% else %}                                                                                      #
      G0 X{printer.configfile.settings.stepper_x.position_endstop + backoff_distance}               # Set X axis position to remove offset incurred from sensorless homing
    {% endif %}                                                                                     #

    {% if homing_current != 0.0 %}                                                                  # Check if a homing_current was configured

      {% if 'tmc2209 stepper_x' in printer %}                                                       # If a homing current was configured, figure out the driver type for X
        {% set driver_x = 'tmc2209' %}                                                              # and define them as driver_x
      {% elif 'tmc5160 stepper_x' in printer %}                                                     #
        {% set driver_x = 'tmc5160' %}                                                              #
      {% elif 'tmc2130 stepper_x' in printer %}                                                     #
        {% set driver_x = 'tmc2130' %}                                                              # https://www.klipper3d.org/Config_Reference.html#tmc-stepper-driver-configuration
      {% elif 'tmc2660 stepper_x' in printer %}                                                     # All drivers at the address above containing SGTHRS or SGT configurations
        {% set driver_x = 'tmc2660' %}                                                              # are checked here
      {% elif 'tmc2240 stepper_x' in printer %}                                                     #
        {% set driver_x = 'tmc2240' %}                                                              #
      {% endif %}                                                                                   #
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

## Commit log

2024-06-09 Add CADs and STLs
    [15.8mm_oct_spacer.STEP, 8mm_oct_spacer.STEP, STH-36_sherpa_mini_mounting_plate_overmold_strain.STEP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]
2024-06-09 Add klipper config
    [Sensorless-Homing.cfg, base.cfg, foxchanger.cfg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]
2024-06-09 Update config
    [printer.cfg]
2024-06-16 Improve toolhead position restore path
    [foxchanger.cfg]
2024-06-17 Improve toolchange patch, allow specify target position after toolchange
    [foxchanger.cfg, tool_0.cfg, tool_1.cfg]
2024-06-18 Improve purge line, fix initial tool change
    [printer.cfg]
2024-06-22 Fix nozzle temp issue when filaments have different temp
2024-06-22 Check initial active tool using switch, and ensure tool is properly detached & attached during tool change
    [foxchanger.cfg, printer.cfg, tool_0.cfg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]
2024-06-22 Extrude more during purge line
    [printer.cfg]
2024-06-30 Update dock design and make latch fits tighter
    [head_holder.STEP, latch.STEP, latch_press.STEP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]
2024-09-28 Improve the fitness of magnets on dock and toolhead
    [dragon_burner_back_plate.STEP, head_holder.STEP, toolchanger.STEP]
2024-10-02 Update latch so the metal pins won't be pushed out during tool change
    [latch.STEP, toolchanger.STEP]
